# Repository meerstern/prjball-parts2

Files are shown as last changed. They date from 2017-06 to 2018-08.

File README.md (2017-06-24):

# prjball-parts2
Component Parts for ProjectionBall v5.X &amp; ProjectionBall  IoT

## 特徴 Feature
  * スマートフォンやPCからWifi経由で遠隔操作可能  You can control through phone or tablet.  
  * アナログ時計、デジタル時計を内蔵  The device has watch functions, digital and analog.  
  * 任意の文字列を表示可能(最大32文字、フォント内蔵)  The device has fonts. You can draw your favorite strings.  
  * 直径が10cm(旧モデル12cm)と一回り小さく  The diameter of this device is 10cm, it's smaller than previous one.   
  * Wifiはアクセスポイントモード、サーバモードの両対応  The wifi module has two modes, AP mode and server mode.  
  
## 関連リンク Related Links
  * ProjectionBall V5.X &amp; IoT [Firmware&Sourcecode][1]      
  * ProjectionBall V5.X &amp; IoT [STL Data&Gerber Data][2]  
  * ProjectionBall V5.X &amp; IoT [Wifi Module Sourcecode][3]  

  * Documents in English are in preperation.  
  * Please click Like button of [Projection Ball Page][4]. 
  
  License - MIT

  [1]: https://github.com/meerstern/prjball-firmware2 "*1"
  [2]: https://github.com/meerstern/prjball-parts2 "*2"
  [3]: https://github.com/meerstern/prjball-wifimodule2 "*3"
  [4]: https://www.facebook.com/projectionball "*4"

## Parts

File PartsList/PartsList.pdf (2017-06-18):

No. | Name | CNT | Memo | Link
1 | JST2PH10 Cables with PH Connector | 3 | Motor Cable& Laser | http://akizukidenshi.com/catalog/g/gC-05683/
2 | L-angle Pin header | 2 | | http://akizukidenshi.com/catalog/g/gC-01627/
2 | FA-130 Brushed Motor | 2 | Motor | https://www.sengoku.co.jp/mod/sgk_cart/detail.php?code=7BGF-TSM4
3 | Jumper | 2 | Wifi RX,TX
4 | CR2032 | 1 | RTCBattery
5 | Red Laser Module | 1 | | http://akizukidenshi.com/catalog/g/gM-00765/
6 | Mirror | 2 | Daiso Dental Mirror
7 | Cube Block　26xM6 | 2 | Mirror Anchorage | http://akizukidenshi.com/catalog/g/gP-07307/
8 | Brace | 2 | | https://www.sengoku.co.jp/mod/sgk_cart/detail.php?code=EEHD-0S35
9 | Bis M2.6x4 | 2
10 | Magnet　fai8x2 | 2 | Radial Magnet direction | https://www.26magnet.co.jp/webshop/cart.php?FORM_mode=view_goods_detail&FORM_goods_id=NE099
11 | Band | 5
12 | Sponge with Tape | 4 | D4mm x W15mm x L4M
13 | Acrylic Sphere 10cm | 1 | | http://amzn.asia/dPmUUdK
14 | Stand | 1 | | https://www.monotaro.com/p/0292/2376/?displayId=4
15 | USB Cable | 1 | | http://akizukidenshi.com/catalog/g/gC-09314/
17 | Capacitor 50V0.1uF | 2 | Noise protect for motor
*No.7,8,9 are not required when you use 3D ptinted mirror module, but two M3 Screw Nuts and two M2.6x6 bis.

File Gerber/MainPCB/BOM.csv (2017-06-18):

Elecrow PN | Parts | Value | Package | QTY | Digikey/Mouser/Manufacturer Part | Remark/ Link
 | JP6,JP11,JP12 | PH�@Male | THT | 3 | 455-1704-ND | Directions are written in silk pattern.
 | BT1 | BOX | CR2032V | 1 | 855-S8401-46
 | D1 | Diode | SMA | 1 | 863-MBR130T3G
C1644 | C1,C2 | 12p | 1608 | 2
C14663 | C7,C8,C9,C13,C14,C15,C16,C17,C18,C20,C5,C6,C3 | 0.1u | 1608 | 13
 | IC1 | 3.3VREG | v-reg-DPACK | 1 | 511-LF33CDT-TR
4040806A | LED1 | BULE | 1608 | 1
4041105A | LED2 | ORANGE | 1608 | 1
 | R5,R6 | VR | SMD | 2 | 81-PVZ3A472C01R00
C25804 | R7,R8,R9,R10,R14,R19,R20,R22,R4 | 10k | 1608 | 9
C21190 | R11,R12,R13,R21,R23,R24,R25,R26 | 1k | 1608 | 8
 | S1 | switch-TL3XYO | 1 | 612-EG1218
6030916A | JP5,JP13,JP15,JP16 | pinhead-1X02 | 4
 | U1 | STM32F373CB | LQFP-48 | 1 | 511-STM32F373CBT6
 | U2 | WIFI | ESP-13-WROOM-02 | 1 |  | Reauire a certification mark of conformance to technical standards in Japan.
 | Y1 | FC-135/32.K | ECS-31B_xtal | 1 | 732-FC135-32.76KAA3
 | C12 | 1000u | 810 | 1 | 647-UUD0J102MNL
 | C19 | 680u | 1010 | 1 | 647-UWT1A681MNL1GS
 | IC2 | DRIVER | SSOP24 | 1 | 757-TB6612FNGC8EL
 | S2,S3 | sw | THT | 2 | 688-SKHHBV
 | Q1 | NFET | SOT23 | 1 | 942-IRFML8244TRPBF
 | M2 | mSD | SMD | 1 | 798-DM3ATSFPEJM511
C15850 | C10,C11,C23 | 10u | 2012 | 3
 | F1 | PTC | 1812 | 1 | 507-1770-1-ND
 | M1 | uUSB CON | SMD | 1 | 649-10118194-0001LF

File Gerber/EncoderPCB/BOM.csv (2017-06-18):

Elecrow PN | Parts | Value | Package | QTY | Digikey/Mouser/Manufacturer Part | Remark/ Link
 | C2 | 0.1uF | 1608 | 1 | Free Components | 15331 | C14663
 | R1,R2,R3,R4,R5,R6 | 0 | 1608 | 6 | Free Components | 21903 | C21189
 | IC1 | AS5048A | TSSOP14 | 1 | AS5048A-HTSP-500CT-ND | http://www.digikey.jp/product-detail/ja/ams/AS5048A-HTSP-500/AS5048A-HTSP-500CT-ND/3188617

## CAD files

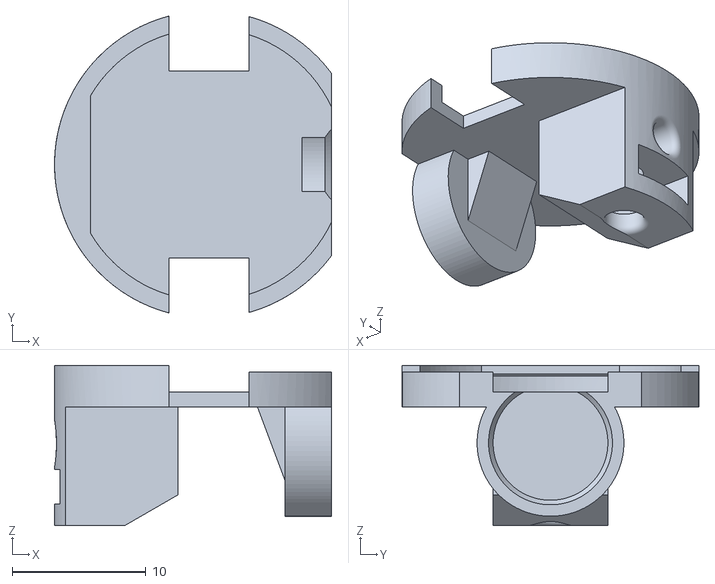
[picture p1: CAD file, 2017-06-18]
3DParts/mirror-module.stl
20.8 x 22.2 x 12.0

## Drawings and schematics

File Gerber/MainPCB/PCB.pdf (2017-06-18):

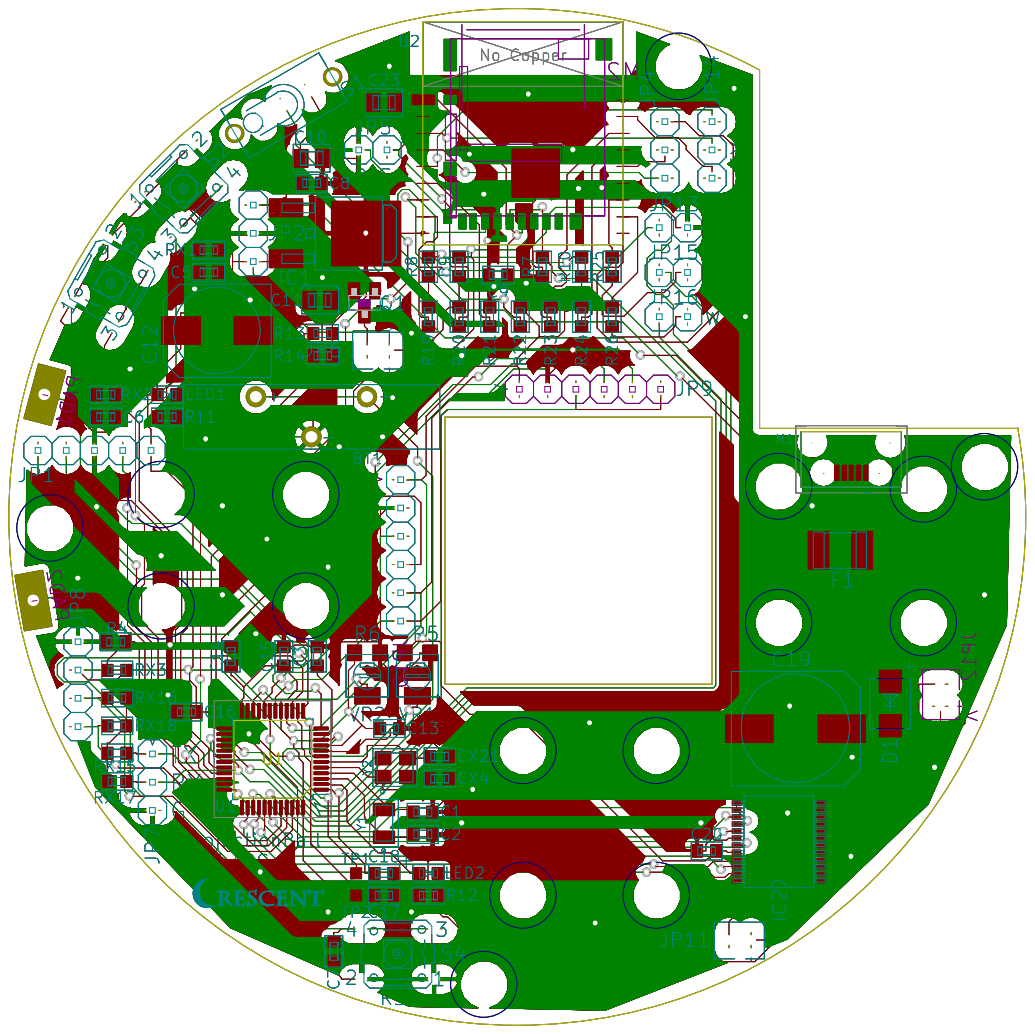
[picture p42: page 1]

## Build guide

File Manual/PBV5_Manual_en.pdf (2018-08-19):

# Projection Ball IoT

v5.4S

# User’s Manual

Revision
st 1 | 2017/04/19 | First release
nd 2 | 2017/6/10 | Add the way of adjustments

ProjectionBall Manual | 2

## Contents

1. Overview

Thank you for purchasing ProjectionBall this time. Please read this instruction manual carefully

and use it correctly.

It is a compact laser projector that anyone can use a laser projector which has been used only in

limited fields such as outdoor events by applying robot engineering technology at low cost.

ProjectionBall is a vector type simple laser projector. Drawing information is recorded at the time of

shipment, so you can draw immediately, such as stars and arrows.

By connecting the SD card slot, inserting the SD card with the data written in it, you can draw data

of your desired drawing shape from the SD card.
With the Wifi module (ESP - WROOM - 02), you can switch drawing from switching from smartphone

or PC to ProjectionBall, perform arbitrary character display, time adjustment, Wifi access point

setting etc is.

There is a Uart port shared with the Wifi module on the main body of ProjectionBall. You can also

operate ProjectionBall by connecting to Arduino, RaspberryPI etc via Uart port.

2. Safety Precautions

2-1. Prohibited items
◆ Prohibition of direct lighting of laser light

Although we are using a relatively safe laser module with class 2 output less than 1 mW, there is a

risk of loss of vision or loss of vision in direct viewing.

◆ Prohibition of projection to animals, people, especially head

We use a relatively safe laser module with class 2 output less than 1 mW, but if laser light enters the

eye directly, there is a danger of loss of vision or blindness.

◆ Supplied from PC USB power supply

Although USB connector is used as power supply, please never connect to PC. There is a possibility

that noise such as a motor etc. will enter the personal computer side and cause personal computer

malfunction.

2-2. Precautions

Do not use the USB power supply of output 1A or less

Operating power becomes insufficient, operation becomes unstable, it may cause breakdown at the worst. Please connect to USB charging adapter etc. (voltage 5 V, current 1.2 A or more).

◆ Please disconnect USB power after use

To prevent malfunction, please be sure to unplug the USB power supply or USB connector part after

use.

◆Please pay attention to strong magnets

A powerful neodymium magnet is used for the position detection in the mirror module part. There is

a possibility that it may cause trouble if it is brought close to a magnetic card or other equipment, so

please be careful about handling it.

◆ Place only drawing data on the SD card

When using the SD card please put only the drawing data in the card. In some cases, data in the card

may be damaged. Please do not use SD card with important data. Also, please use SD card with no

problem even if it is damaged.

3. Features

It is a compact laser projector that anyone can use a laser projector which has been used only in

limited fields such as outdoor events by applying robot engineering technology at low cost.

ProjectionBall is a vector type simple laser projector that can draw simple geometric figures and

alphanumeric characters. Because it uses a relatively safe laser light source, it is possible to project a

projection distance of about 1 m ahead in a bright place and about 5 m in a dark place.

◆ Excellent visibility

Because you are using a laser, you do not need to darken the room like a liquid crystal projector.

It is possible to draw clearly even in bright places.

◆ Design and functionality

Depending on the shape of the ball, it is possible to draw it anywhere you want, such as floor, wall, or

ceiling, in any orientation you like.

It operates with USB power supply and it is possible to draw for several hours with a mobile battery

for smartphone.

◆ Extensibility

By drawing any shape from the SD card and connecting it with a device such as RaspberryPI, it

becomes possible to draw your favorite figure at any time.

◆ Versatility

Not limited to the interior of the room, the application is infinite, such as digital signage such as

show window and reception, utilization as IoT display by other equipment cooperation, information

display by incorporating in the robot.

4. Specification
※ It may be changed
- Power supply 5 V, maximum 1.2 A microUSB terminal (Please supply from general purpose USB

power supply)

- Frame rate 5 to 15 fps (Depending on the number of coordinates, repeat number setting)
- Resolution mirror angle 9 degrees / 400 bit
- 10 types of built-in drawing data
- Alphanumeric display function (Scroll up to 30 characters maximum)
- Analog / digital clock, date display function
- SD card memory drawing (Maximum number of coordinates 200 points, up to 10 data can be

supported by switch switching)

- Micro SD card slot
- 3.3 V red 1 mW or less Class 2 laser module
- Blue power LED
- With Uart debug port (9600 bps, 3.3 V)
- Setting, time keeping function (backup battery CR 2032)
- Wifi module installed
- Capacitive touch sensor mounted

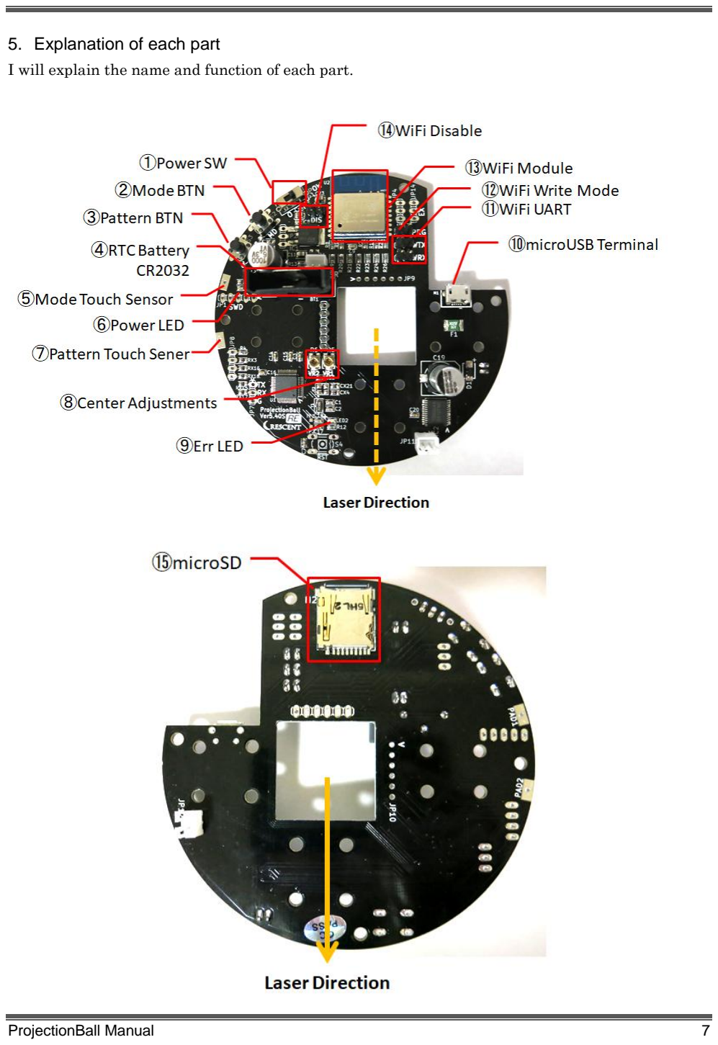
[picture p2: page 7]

5. Explanation of each part

I will explain the name and function of each part.

①Power switch

[0] turns OFF, [I] turns ON.

② Mode button

Switch on the mode such as constantly lighting,

strokes writing, clock etc.
③ Pattern button

Switch drawing patterns such as stars and

arrows.
④ Backup battery

Backup battery to store mode, pattern, character

string, time information.
⑤ Mode touch sensor

You can switch modes by touching a sphere. ⑥ Power LED

Blue lights up when the power is on.
⑦ Pattern touch sensor

Pattern can be switched by touching a sphere. ⑧ center adjustment trimmer

It is for adjusting the center axis of the mirror.

Please do not touch except when trouble such as

chipping occurs.
⑨ Error LED

It lights up when it stops automatic when there

is a problem with the mirror module or motor

part.

⑩ microUSB terminal

It is microUSB terminal for power supply. Please

use a power supply capable of supplying voltage

5V and current 1.2A.
⑪ WiFi UART pin

It is a jumper pin connecting the control

microcomputer and ESP - WROOM - 02.
⑫ WiFi write mode pin

When shorting the jumper and turning on the

power, ESP - WROOM - 02 goes into write mode. ⑬ WiFi module

It is ESP - WROOM - 02 which provides WiFi

function.
⑭ WiFi invalidation pin

Shorting off WiFi radio waves. It is used when

you want to invalidate WiFi communication in

environments where radio wave communication

is not permitted.
⑮ micro SD slot

Insert microSD containing data when drawing

from data created with drawing software.

6. How to use

This section explains how to prepare for using ProjectionBall.
① Assemble the stand. The side with the sponge will be on the upper side.

② Install the ProjectionBall main unit on the stand.

Check the laser irradiation destination. It is irradiated from the opposite part to the Wifi module.

If the ProjectionBall board is not set in the sphere, please set through the spherical cable hole with

the USB cable connected as shown below.

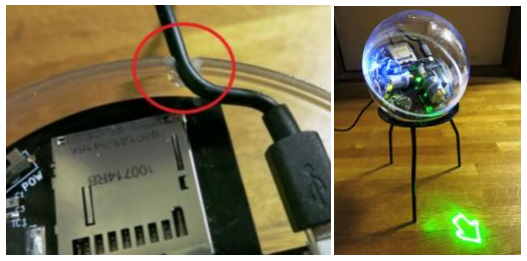
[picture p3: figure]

③Connect the USB power supply. Please use a USB power supply that can output a current of at

least 1.2 A with a voltage of 5 V.
④ The blue LED indicating power ON lights up, and drawing starts. If the blue LED does not light

up, check that the power switch on the Projection Ball main unit is ON.
⑤ To switch the drawing mode, touch the ProjectionBall main unit, the upper left, the mode touch

sensor near the palm. You can also press the mode button.

Lissajous mode → rotation mode → single stroke writing mode → continuous drawing mode →

analog watch mode→ digital watch mode → date display mode → character string display mode

Touch in this order to toggle.
⑥ To switch the drawing pattern, touch the ProjectionBall body, bottom left, touch the pattern touch

sensor with your palm. It is the same even if you press pattern button.

Star → arrow → e-mail → smile → sun → cloud → umbrella → snow → thunder

Touch in this order to toggle.

* When the microSD card containing the drawing data is inserted, the drawing data changes.
⑦ To temporarily stop drawing, touch the ProjectionBall body, upper left and lower left with the

palm at the same time. Touch the upper left and lower left with the palm again at the same time to

resume drawing. It is the same also with simultaneous pressing of pattern button and mode button. ⑧Turning the power ON while simultaneously holding the pattern button and pattern button

disables the touch function. If you turn on the power again while simultaneously pressing it, the

touch function will be activated.

7. Wifi connection method

ESP - WROOM - 02 for WiFi communication to the ProjectionBall main body is carried. It supports

two modes, server mode not via access point and client mode connecting via access point.

When it is used for the first time or when the configured access point can not be found, it is automatically connected directly (server mode). If a configured access point is found, it will

automatically go through the access point (client mode).

7-1. Server mode connection method
①Turn on the power of the Projection Ball.

When it is used for the first time or when the configured access point can not be found, it will

automatically enter the server mode in tens of seconds.
② Connect from the smartphone, PC, etc. to the access point name "prjballXX".

* The XX part is a unique alphanumeric character of a part of the MAC address of ESP - WROOM -

02.
③ Enter "192.168.4.1" to the address screen of the browser etc and press "Enter" key.

④ Connection is completed when "ProjectionBall Remote" screen is displayed.

※ Since the access point "prjballXX" is not connected to the Internet, the first connection on the

iPhone or Android smartphone may be disconnected immediately. Please repeat the connection

several times.

7-2. Client mode connection method
① Connect in advance in the above server mode and display "ProjectionBall Remote" screen.

② To connect via the access point, set "SSID" and "PASS" on the "Wifi" tab.

③ After completing the access point setting, it will be connected via the access point when the power

is turned on again.

* To connect via the access point, turn off the power of the Projection Ball once, then turn it on

again.

After several tens of seconds, we will automatically try to connect to the access point we set earlier.

If the connection is successful, you can operate from a browser such as a smartphone or PC

connected to the same access point.
④ On the address screen of the browser such as smartphone or PC

Type "prjballxx.local" and press "Enter" key. The XX part of prjballXX is the same as the XX part of

prjballXX of the access point name. The XX part is a unique alphanumeric character of a part of the

MAC address of ESP - WROOM - 02.
⑤ When "ProjectionBall Remote" screen is displayed, connection is completed.

If you want to connect again in the server mode, set appropriate characters with "SSID" and

"PASS" on the "Wifi" tab. .
※ Since you can not find an access point by entering appropriate characters, it will be in server

mode

7-3. ProjectionBall Remote How to use

I will explain how to use "ProjectionBall Remote" screen.

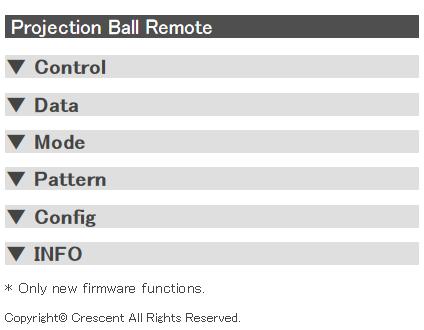
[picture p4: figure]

Immediately after displaying the "ProjectionBall Remote" screen, it is displayed in six categories:

"Control" "Data" "Mode" "Pattern" "Config" "Info".

◆ "Control" category

- "Start / Stop"

Please press "Stop" to pause drawing and "Start" to resume.

- "Angle"

It is used to change the drawing angle.

Enter the angle in the range of 0 to 359 °.

The angular resolution is 3 °.

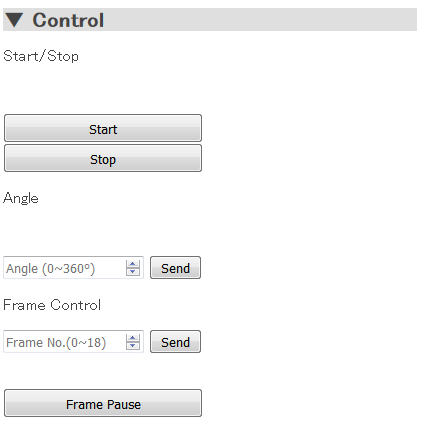
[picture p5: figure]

◆"Data" category

- "Internal / Memory Data"

To draw from the built-in drawing pattern, press "Internal Data".

To draw from the microSD containing the drawing data, press "Memory Data".

* If microSD is not inserted or drawing data is not inserted, drawing will stop when "Memory Data"

is pressed.

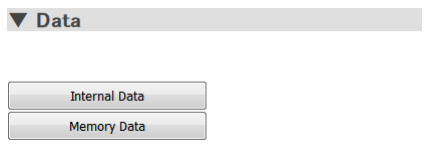
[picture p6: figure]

◆"Mode" category

- "Animation"

-MicroSD No card: Lissajous curve drawing
- With microSD card: animation drawing (frames **. Csv files are read in order)
- "Rotation"

It is a mode to draw while rotating.

- "One-stroke"

It is a mode to draw with a single stroke.

- "Always-on"

It is a mode to draw data all the time.

- "Analog Watch"

This mode displays the analog clock.

- "Digital Watch"

This mode displays the digital clock.

- "Date"

It is a mode to display the date.

- "String"

This mode displays alphanumeric character strings. The initial value is "Hello".

You can draw an arbitrary character string by filling in "String" field and pressing "Send" button.

* If it is more than 6 characters it will be automatically scrolled and rendered.

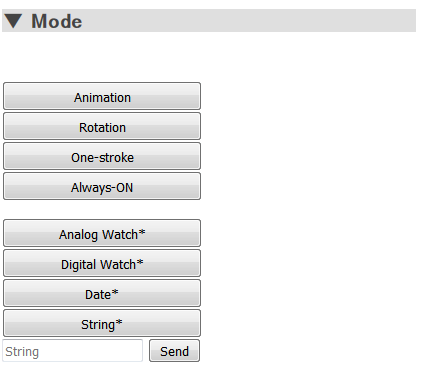
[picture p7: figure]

◆"Pattern" category

Drawing stops if there is no corresponding drawing data even with microSD card.

- "Star / Data 0"

-MicroSD card absent: The star of the built-in data is drawn.

-Micro SD card present: data0.csv file will be drawn.

- "Star / Data 0"

-MicroSD card absent: The star of the built-in data is drawn.

-Micro SD card present: data0.csv file will be drawn.

- "Arrow / Data 1"

-MicroSD card absent: Arrow of internal data will be drawn.

-Micro SD card present: data1.csv file will be drawn.

- "Mail / Data 2"

-MicroSD card absent: Mail of internal data will be drawn.

- With microSD card: data2.csv file will be drawn.
- "Smile / Data 3"

-MicroSD No card: Smile of internal data will be drawn.

-Micro SD card present: data3.csv file will be drawn.

- "Sun / Data 4"

-MicroSD card absent: The sun of the built-in data is drawn.

-Micro SD card present: data4.csv file will be drawn.

- "Cloud / Data 5"

-MicroSD card absent: Cloud of built-in data will be drawn.

-Micro SD card present: data5.csv file will be drawn.

- "Rain / Data 6"

-MicroSD card absent: umbrella of internal data will be drawn.

-Micro SD card present: data6.csv file will be drawn.

- "Snow / Data 7"

-MicroSD card absence: snow of built-in data is drawn.

-Micro SD card present: data7.csv file will be drawn.

- "Thunder / Data 8"

-MicroSD card absence: Lightning of built-in data will be drawn.

-Micro SD card present: data8.csv file will be drawn.

- "Heart / Data 9"

-MicroSD card absent: Heart of built-in data will be drawn.

- With microSD card: data9.csv file will be drawn.

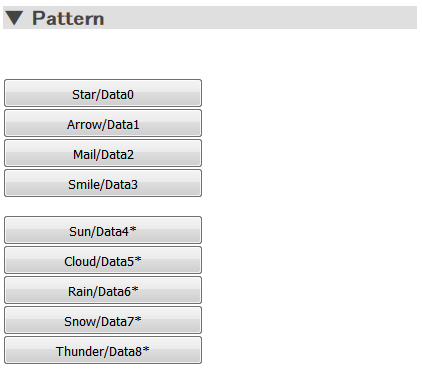
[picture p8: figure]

◆"Config" category

Set WiFi module access point settings, date and time.

- "WiFi AP Mode Setting"
Connect using the access point Set the access point name (SSID) and password (PASS) when using

client mode. After inputting and pressing "SAVE", the setting is saved.

- "Set Date"

To set the date, press "Send". The dates acquired from browsers such as smartphones and PCs are

automatically entered.

* If the date is not displayed properly, check the date of the smartphone or PC you are operating.

- "Set Time"

To set the time, press "Send". Time is automatically entered from the browser such as smartphone or

PC.

* If the time is not displayed correctly, check the time of the smartphone or PC you are operating.

◆"Info" category

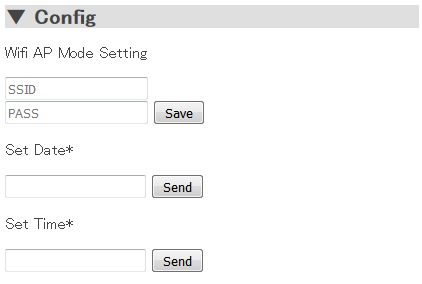
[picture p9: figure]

The Wifi module version and Web site link are displayed.

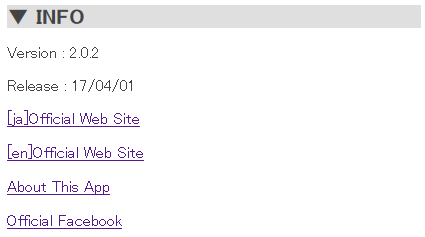
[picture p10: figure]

8. Optional data drawing method

You can draw drawing data on the SD card, slot it on the board, and draw arbitrary shapes.

8-1. SD card drawing specification

- When the SD card is not inserted, it will automatically draw from the internal memory data of the

main unit.

- If an SD card is inserted and drawing data is not inserted or if the file is corrupted, an error occurs

and nothing is drawn.

- Pattern drawing specification
- Up to 10 types of drawing can be made by switching pattern switches.
- It is possible to select from 3 types of constantly lit, rotated, and stroked by mode switch switching.
- The maximum number of coordinates per file is 200.
- File name is half-width alphanumeric data0.csv data1.csv data2.csv data3.csv ... data9.csv.
- Animation drawing specification
- By inserting drawing data slightly different from frame 0 to frame ** (maximum ** up to 17)

animation drawing like a flip cartoon becomes possible.

- Insert the file corresponding to the SD card, and place it under the mode switch SW4 or SW5, the

animation drawing will start.

- The maximum number of coordinates per file is 200.
- File name must be half-width alphanumeric, frame0.csv frame1.csv · · · frame 18. csv.
- Approximately every 300 msec, the drawing data will be switched automatically from frame 0 to

frame 1, frame 2 and according to the number of files in the SD card.

- It returns to frame 0 in the last file and it operates iteratively.

8-2. Drawing data creation method

In this section, we will explain the drawing data creation method using dedicated drawing data

creation software.

Please download the drawing software from the following URL.

http://projectionball.jp/share/PBS.zip pass: crescent

- The operating environment is Windows .Net Framework 4.5 or later installed PC
- Launch PBS 2.exe by double-click with no installer required.
- Drawing data creation method using dedicated drawing software
1) Activate the software.
2) Place new coordinates by left clicking and create your favorite shape. Conversely, when deleting,

you can delete the coordinates by right clicking.
3) Please arrange the coordinates finely for curves and complicated figures. Also, please set so that

the starting point and the ending point are close.
4) When finished, save as "File" → "Save As" → "pbs file".

5) Select "File" -> "export csv" -> "data0.csv" and export.
6) Save the "data0.csv" file on the SD card, set it under SW2, SW3 down, SW4 up and SW5, and

when you turn on the power, the figure will be drawn.
※ Note Even if pbs file is saved on SD card, it can not be drawn. Please export the csv file and save it

on the SD card.

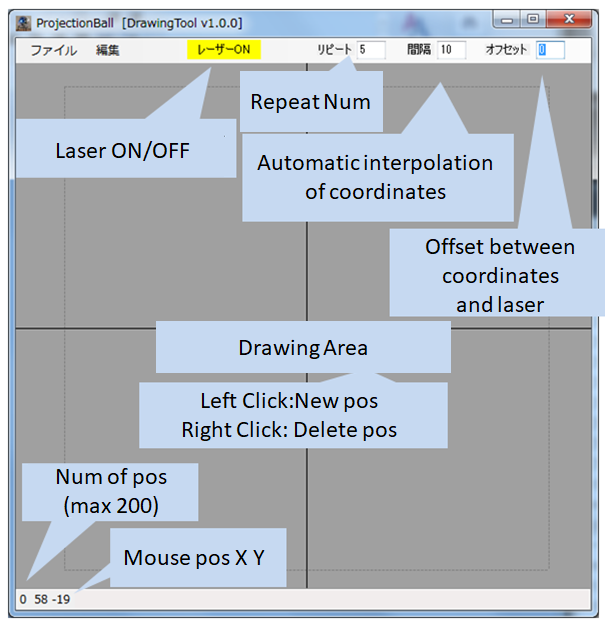
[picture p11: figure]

- As the repeat number increases, the accuracy increases but the frame rate becomes rough.

Conversely, if the repeat number is small, the accuracy will be worse, but the frame rate will rise. If

the repeat number 5 is a standard and complicated figure, set it to 8 to 12. Conversely, in case of

simple figure, set repeat number to 3 ~ 5.

- To move the middle coordinates, hold down the "Ctrl" key and drag the coordinates you want to

move to move the middle coordinates.

- To place new coordinates, hold down the "Shift" key and left click to place the coordinates in laser

OFF mode.

- If the starting point and the ending point can not be located close to each other, click "Laser ON /

OFF", turn OFF the laser lighting, and put the extinct coordinates so that the end point is near the

starting point.

- If there is an image file of the figure you want to draw, place the background with "Edit" →

"Background reading".

* If the size does not match please edit the image file with "paint" etc and resize it.

- If a message with more than 200 drawing coordinates appears at the time of export, reduce the

number of coordinates or set the interval to a larger value such as 10 to 20 of the initial value.

- On the improvement of accuracy of drawing data
- If you want to draw at sharp corners, arrange the corner part coordinates a few times consecutively

and place them at the same place and the corners will be drawn cleanly.

- It is also possible to draw beautifully by making the acute angle part circle around and letting the

detour part "laser off".

8-3. Drawing data specification

Describe the specification of drawing data. The csv file created with dedicated drawing software

meets the following specifications. Please refer if you do not use special drawing software.

- In the first line, enter the numerical value for drawing definition. In the first row and the first

column, enter the repeat number.

Please enter 0 for 1st row 2nd row, 3rd row. If 5 is standard and complicated figure, set it to 8 ~ 12.

For simple figures, set the repeat number to 3 ~ 5.

- As the repeat number increases, the accuracy increases but the frame rate becomes rough.

Conversely, if the repeat number is small, the accuracy will be worse, but the frame rate will rise.

- From the 2nd line, enter coordinate data with half-width numerals.
- The first row indicates whether or not the laser is lit, 0 is off, and 1 is lit.
- The second row is the X coordinate and the third row is the Y coordinate.
- Create coordinates with a maximum (± 150, ± 150) around (0,0) as a guide.
- When the drawing starts, the laser light moves from the 2nd line to the 3rd line and the 4th line

sequentially.

- If you find a blank space, judge it as the last data, go back to the second line and start drawing

again.

* In the case of dedicated drawing software, it automatically becomes data according to the following

rule

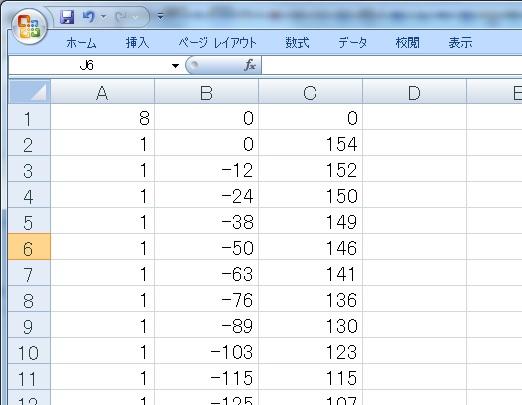
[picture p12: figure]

9. How to rewrite WiFi module

ESP - WROOM - 02 for WiFi communication to the ProjectionBall main body is carried. The factory

shipped ESP - WROOM - 02 code is published on the following site. If necessary, you can also update

your ESP - WROOM - 02 or add your own code by adding it.

https://github.com/meerstern/prjball-wifimodule 2

Also, IO pins other than the RX and TX ports used in ProjectionBall can be accessed from the

external EX port. It is possible to connect LED and serial communication equipment separately as

necessary.

9-1. Arduino development environment preparation

We use the Arduino development environment when updating the firmware of ESP - WROOM - 02 or

incorporating your own code.
① Install the Arduino development environment on the PC.

② Activate the Arduino development environment and click "File" → "Development environment".

③ Add the following URL to "Additional Board Manager URL" on the "Settings" tab.

http://arduino.esp8266.com/stable/package_esp8266com_index.json

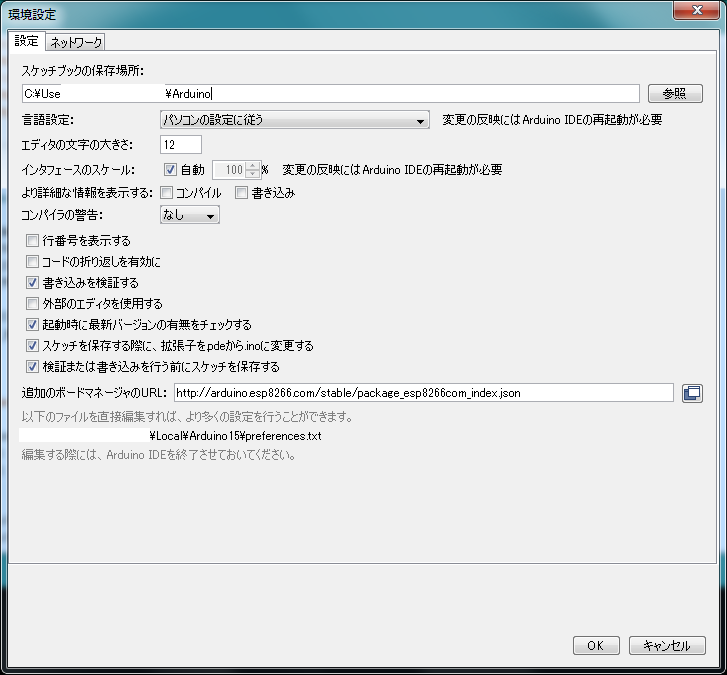
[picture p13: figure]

④Scroll from Tools -> Microcomputer Board -> Board Manager to the bottom, select 'esp 8266 by

ESP 8266 Community' and click Install.

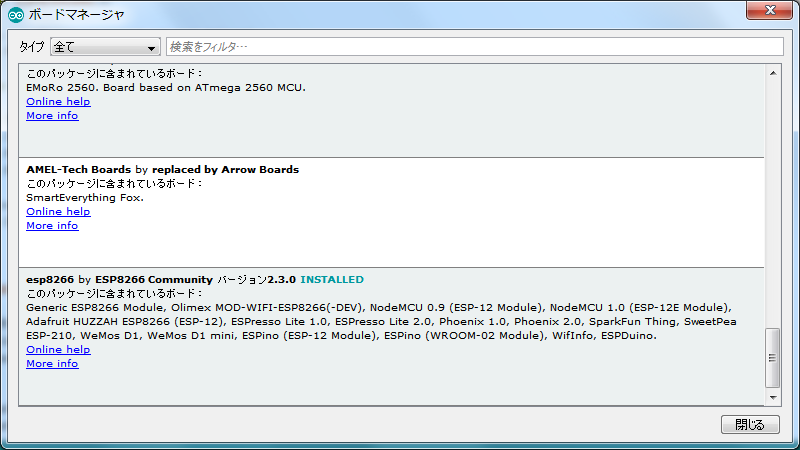
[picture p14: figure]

⑤Click "Tools" → "Microcomputer board" → "Generic ESP 8266 Module".

⑥ Perform the setting as described below in "Tool" → "Microcomputer board".

The serial port selects the serial port connected to ESP - WROOM - 02 at the time of writing.

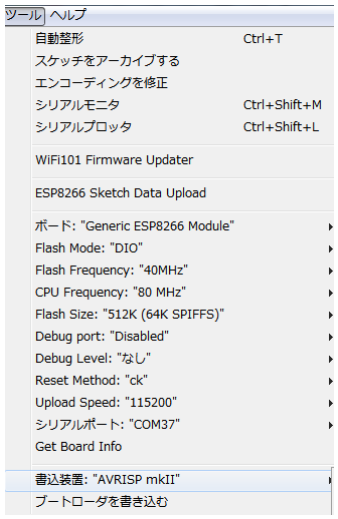
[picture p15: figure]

9-2. Writing from the Arduino development environment

When writing the firmware from Arduino development environment to ESP - WROOM - 02, a USB

serial conversion module etc is required. Please prepare separately.
USB serial conversion module (AE-FT 234 X) http://akizukidenshi.com/catalog/g/gM-08461/

① Remove the jumper pin to WiFi UART TX pin and WiFi UART RX pin,

Connect the USB serial conversion module to the ESP - WROOM - 02 of the Projection Ball main

unit. In case

Connect the GND of the USB serial conversion module to the WiFi UART GND pin.

Connect the USB serial conversion module TX to the WiFi UART RX pin.

Connect the USB serial conversion module RX to the WiFi UART TX pin.

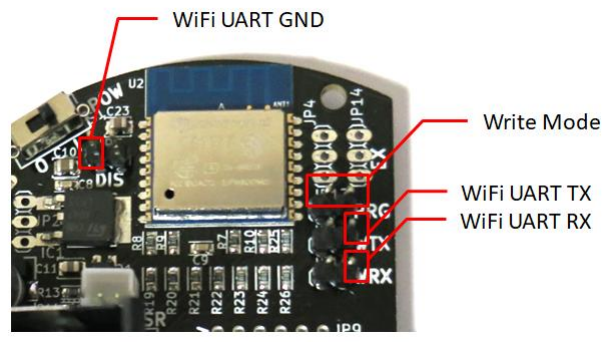
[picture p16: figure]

②Confirm the port number of the USB serial conversion module from the device manager etc.

③ Download the latest WiFi module firmware code from the site below and open the "ESP8266.ino"

file.

https://github.com/meerstern/prjball-wifimodule 2
④ Set the port number of the USB serial conversion module.

Select the connection destination port from "Tools" → "Serial port".
⑤ Connect the jumper to the write mode pin and short the write mode pin.

⑥ Power on the Projection Ball body.

⑦ Press the write button to write the farm.

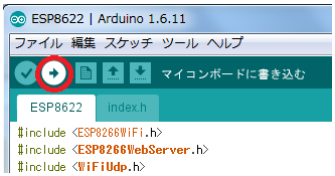
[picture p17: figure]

⑧It is update when writing is completed.

In case of first time writing, an error may appear.
If you get an error please try again while confirming the work from ①.

⑨ Set the jumper pin to WiFi UART TX pin (WiFi UART RX pin if necessary).

10. External device linkage method

By sending commands from the UART port of ProjectionBall to the UART port of another device, it is

possible to switch the drawing pattern and drawing mode, pause the drawing, and reread the

drawing data.

If necessary, connect pinhaders and wiring and connect to other equipment. Connect the TX on the

board to the RX terminal of another device, the RX on the board to the TX terminal of another device,

and also connect the GND.
When sending a command from a PC etc., use a USB serial conversion module (AE - FT 234 X

http://akizukidenshi.com/catalog/g/gM-08461/ ) etc and send a command using COM software such as

Teraterm please.
After sending the command, the command is executed by sending the return key (line feed). The

voltage of UART is 3.3V. It is different from RS232C. Also, please set the baud rate to 9600 bps.

* In the case of external device linkage, since the UART ports conflict, the command command from

the WiFi module can not be used.

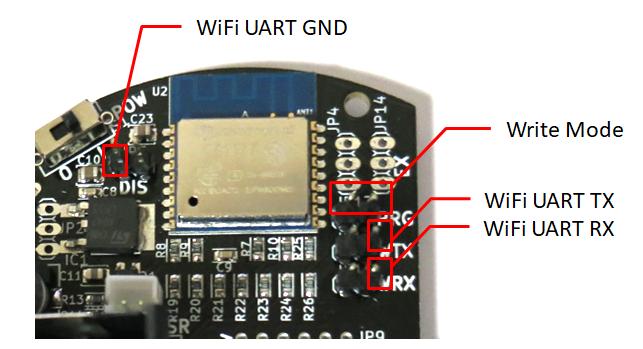
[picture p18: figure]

Table 1 UART Command lists

Command Name | Uart command | Description
Start | srt | When drawing is stopped by a command, it is used again when restarting.
Stop | stp | It is used to stop drawing.

Pattern0 | sw0 | No SD card star pattern, with SD card data0.csv drawing
Pattern1 | sw1 | No SD card arrow pattern, with SD card data1.csv drawing
Pattern2 | sw2 | No SD card mail pattern, with SD card data2.csv drawing
Pattern3 | sw3 | No SD card smile pattern, with SD card data3.csv drawing
Pattern4 | sw4 | No SD card sun pattern, with SD card data4.csv drawing
Pattern5 | sw5 | No SD card cloud pattern, with SD card data5.csv drawing
Pattern6 | sw6 | No SD card rain pattern, with SD card data6.csv drawing
Pattern7 | sw7 | No SD card snow pattern, with SD card data7.csv drawing
Pattern8 | sw8 | No SD card thunder pattern, with SD card data8.csv drawing
Pattern9 | sw9 | No SD card heart pattern, with SD card data9.csv drawing
Analog Clock | awt | Switch to analog clock display mode.
Digital Clock | dwt | Switch to digital clock display mode.
Date Mode | dym | The date display mode is switched.
String Mode | stm | Switch to arbitrary character string display mode.
String Set | stg=X | Arbitrary alphanumeric characters are displayed by placing an alphanumeric character string in X. X can be up to 30 characters.
Time Set | tim=XXYYZZ | Set the time via the UART. Example tim = 213000 21h:30m:00s
Time Get | tim? | Currently, the time held inside ProjectionBall is returned in UART.
Date Set | day=XXYYZZ | Set the date via UART. Example day = 170401 17’April, 1st
Date Get 令 | day? | The date currently held in ProjectionBall is returned in UART.
Animation Mode | frm | No SD card :Lissajous curve With SD card : animation (frame **. Csv) will be.loaded.
Rotate Mode | rot | Switch to the rotating animation drawing mode.
Stroke Line Write Mode | str | Switch to the stroke writing animation drawing mode.
Always Lighting Mode | alw | It switches to the drawing mode that always lights up.
Center Position Setting | cen=X,Y | By inserting numbers into X and Y, it is a command to move relative to the current drawing coordinate center. If you set a large value, drawing may not be done correctly. Examples cen = 20, -30
Angle Setting | deg=X | By inserting a value from 0 ° to 360 ° in X, this command rotates the drawing figure at 3 ° intervals. Example deg = 135
Reload | rst | This command executes reading again when the SD card is replaced.
Frame Specification | fno=X | By placing a value between 0 and 18 in X, we draw the frame of the specified animation.
Animation Drawing Frame Pause | fpa | Stops automatic feeding of drawing data when animation is drawn. By running the same command again, automatic feed is restarted.

11. Laser module specification

In terms of safety, we are using a red laser module with 3.3 V drive that is less than 1 mW. When

replacing with another laser module, the same 3.3 V laser module can be used. The maximum

current that can be supplied is 250 mA as designed. We can not support problems and failures due to

the use of laser modules other than standard products.

12. Adjust / Troubleshoot

When trouble etc. occurred, please refer to the following. ◆ The power LED lights, but drawing does not start

- In case of pause mode, release it

Touch the ProjectionBall body, upper left and lower left with the palm at the same time. Touch the

upper left and lower left with the palm again at the same time to resume drawing. It is the same also

with simultaneous pressing of pattern button and mode button.

- Check that the current of the USB power supply is sufficient enough.
Please connect to USB charging adapter etc. (voltage 5 V, current 1.2 A or more).

◆ Mode, pattern, time etc. are reset

It is possible to hold for more than a few months without USB power supply.

If mode, time etc. are not maintained, please replace the battery.

Replacement battery CR 2032 x 1 * Please be sure to replace plus / minus polarity with care.

◆ WiFi access point is not displayed, can not connect

- Check that there is no jumper pin on the WiFi invalidation pin of the ProjectionBall main unit.

When a jumper pin is inserted in the WiFi invalidation pin, the radio wave stops and can not be

connected.

- If there are multiple other WiFi radio waves in the vicinity, it may not be possible to connect due to

interference or interference.

Please connect the PC or smartphone closer to the ProjectionBall main unit.

◆ Drawing is lacking

- Make sure that the laser beam strikes the stand, the sphere, etc., and is not blocked.
- The center position of the drawing may be misaligned.

When the drawing center position shifts, the optical axis of the laser interferes with the frame part,

and the drawing is lacking. First adjust the position of the motor and laser module so that the optical

axis of the laser reflects at the center of the mirror. If it still does not come to the center, adjust the

variable resistance.

Adjust the variable resistor VR 1, 2 for drawing center adjustment with the + driver. Adjust the angle, please turn. If the laser beam does not hit the center of the mirror (back side) of the motor 2, adjust the center of the motor 1 (X axis direction) by adjusting VR1. When the laser light emitted

from the motor 2 is caught on the board, adjust the center of the motor 2 (Y axis direction) by

adjusting VR2.

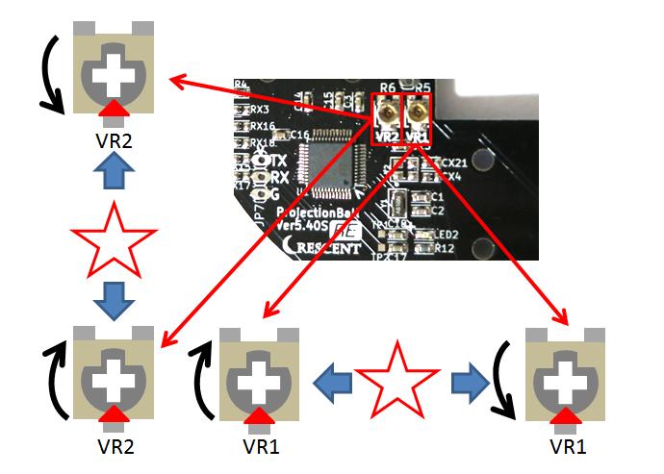
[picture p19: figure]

◆The shape is randomly drawn or the drawing is not clean

- When the current of the power supply is insufficient or the current is limited by the safety circuit of

the USB charging adapter, it may not operate properly. Please try another USB power supply.

- Mirror position Make sure that the center of the magnet matches the center of the encoder IC (black chip of the encoder board). Also check whether the distance between the magnet and the

encoder IC is about 5 mm. On the contrary, if it is too close, contact and magnetic force may be too

strong to draw beautifully.

◆ Error Yellow Lights up and stops

- Make sure that motor 1 and motor 2 are properly connected to the connector. Make sure that the

encoder board is correctly soldered. Also, make sure that the metal of the housing of the laser module

contacts the soldering part of the encoder board and is not short-circuited.

◆ Mirror module magnet position adjustment method

This adjustment has already been done at shipment. Do not remove the magnet from the mirror

module.

In the unlikely event that you remove the magnet from the mirror module, follow the procedure

below to adjust the magnet position.

A neodymium magnet for position detection is installed on the side opposite to the motor shaft mounting part of the mirror module (red frame in the figure below). Unlike ordinary magnets, this neodymium magnet has NS poles separated in the axial direction. The boundary between N pole and

S pole is detected with a sensor and the position is read. If the angle of this magnetic pole is deviated

from the reflection surface of the mirror, it will not be drawn at the intended location.

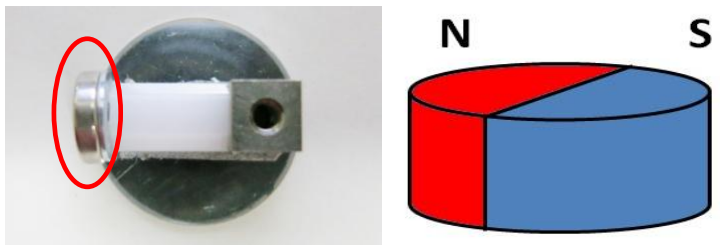
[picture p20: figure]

* If one side is mounted correctly, it is possible to fix the magnet so that the two sides of the

magnet face each other so that the magnets face each other.

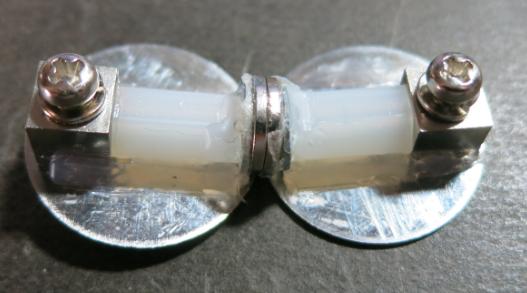
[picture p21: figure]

① Place the mirror module at the center of the azimuthal magnet with the magnet part of the

mirror module facing downward (be careful as the azimuthal magnet goes bad if placed for a

long time).

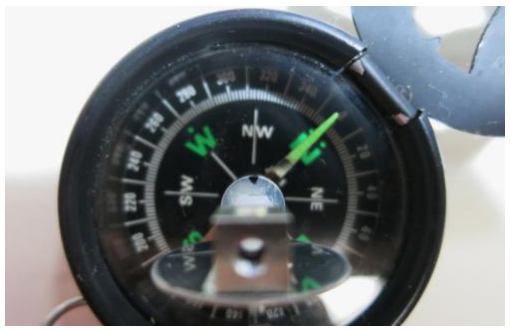
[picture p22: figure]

② As shown in the figure below, rotate the magnet adsorbed by the washer so that the N pole of

the azimuthal magnet faces to the left, and make the angle of the azimuthal magnet coincide with the mirror surface. When the adjustment is completed, fix it with tape).

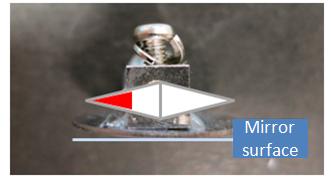
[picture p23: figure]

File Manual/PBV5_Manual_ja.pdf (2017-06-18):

# Projection Ball IoT

v5.4S

# 取扱説明書

改訂履歴

第 1 版 | 2017/04/19 | 新規作成
第 2 版 | 2017/6/10 | 調整方法及び誤字を修正

ProjectionBall 取扱説明書 | 2

目次

1. 概要

このたびは ProjectionBall をお求め頂き、ありがとうございます。本取扱説明書をよくお読みいただき、 正しくご使用ください。
今まで野外イベントなど限られた分野でしか使われていなかったレーザープロジェクタをロボット工 学の技術を応用し、低価格で誰でも使える小型レーザープロジェクタです。 ProjectionBall はベクター方式の簡易レーザープロジェクタです。出荷時に描画情報が記録されている ため、星や矢印などすぐに描画を行うことができます。
SD カードスロットを接続し、データを書き込んだ SD カードを挿入して起動することで、SD カードか ら好きな描画形状のデータを描画することもできます。

Wifi モジュール(ESP-WROOM-02)を搭載しているため、スマートフォンや PC から ProjectionBall へ接 続して、描画切替を行うことや任意の文字表示、時刻調整、Wifi アクセスポイント設定などを行うこと が可能です。

Wifi モジュールと兼用の Uart ポートが ProjectionBall 本体にあります。Uart ポートを介して Arduino や

RaspberryPI 等と接続して、ProjectionBall を操作することもできます。

2. 安全上のご注意

ご使用の前に本章をよくお読みの上、正しくお使いください。

2-1. 禁止事項
◆レーザー光の直視禁止
クラス 2 出力 1mW 以下の比較的安全なレーザーモジュールを使用していますが、直視は視力低下や 失明の危険性があります。

◆動物、人、特に頭部への投影禁止
クラス 2 出力 1mW 以下の比較的安全なレーザーモジュールを使用していますが、直接目にレーザー 光が入った場合、視力低下や失明の危険性があります。

◆パソコン USB 電源から供給禁止
電源として USB コネクタを使用していますが、絶対にパソコンには接続しないでください。パソコン 側にモータ等のノイズが入りパソコン故障の原因となる可能性があります。

2-2. 注意事項
◆出力 1A 以下の USB 電源使用しないこと
使用電力が足りず、動作が不安定になり、最悪、故障の原因となる場合があります。USB 充電用のア ダプタ等(電圧 5V、電流 1.2A 以上)に接続して使用してください。

◆使用後は USB 電源を外してください
誤動作防止のため、使用後は必ず USB 電源もしくは USB コネクタ部を抜いてください。

◆強力な磁石に注意してください
ミラーモジュール部には位置検出のために強力なﾈｵｼﾞﾑ磁石を使用しています。磁気カードや他の機器 に近づけると不具合を起こす可能性がありますので、取扱いに気をつけてください。

◆SD カードには描画データのみ入れること
SD カードを使用する際にはカード内には描画データのみを入れてください。場合によりカード内のデ ータが破損する可能性もあります。大切なデータの入った SD カードを使用しないでください。また、万 一、破損しても問題のない SD カードをご使用ください。

3. 特徴

今まで野外イベントなど限られた分野でしか使われていなかったレーザープロジェクタをロボット工 学の技術を応用し、低価格で誰でも使える小型レーザープロジェクタです。 ProjectionBall はベクター方式の簡易レーザープロジェクタで、簡単な幾何図形や英数字などを描画す ることが可能です。比較的安全なレーザー光源を使用しているため、明るい場所では投影距離は約 1m 先、 暗い場所では約 5m 程度先まで投影することが可能です。

◆優れた視認性
レーザーを使用しているため、液晶プロジェクタのように部屋を暗くする必要がありません。 明るい場所でもはっきりと描画することが可能です。

◆デザインと機能性
ボール形状により、床や壁、天井など好きな向きに好きな場所に描画することが可能です。 USB 電源で動作し、スマートフォン用モバイルバッテリで数時間以上描画することが可能です。

◆拡張性
SD カードから好きな図形を描画することや RaspberryPI などのデバイスとつなげることにより、好 きなタイミングで好きな図形を描画することが可能になります。

◆汎用性
部屋のインテリアに限らず、ショーウィンドウや受付などのデジタルサイネージ、他機器連携による IoT ディスプレイとしての活用、ロボットに組込んで情報表示など用途は無限です。

4. 仕様

※変更する場合があります
・電源 5V、最大 1.2A microUSB 端子(汎用 USB 電源から給電してください) ・フレームレート 5~15fps(座標数、リピート数設定に依る) ・分解能ミラー角 9 度/400bit
・内蔵描画データ 10 種類
・英数字表示機能(スクロールで最大 30 文字程度)
・アナログ/デジタル時計、日付表示機能
・SD カードメモリ描画(最大設定座標数 200 ポイント、スイッチ切り替えで最大 10 データまで対応) ・マイクロ SD カードスロット
・3.3V 赤色 1mW 以下 Class2 レーザーモジュール
・青色電源 LED

・Uart デバッグポート付(9600bps、3.3V) ・設定、時刻保持機能(バックアップ電池 CR2032) ・Wifi モジュール搭載
・静電容量タッチセンサ搭載

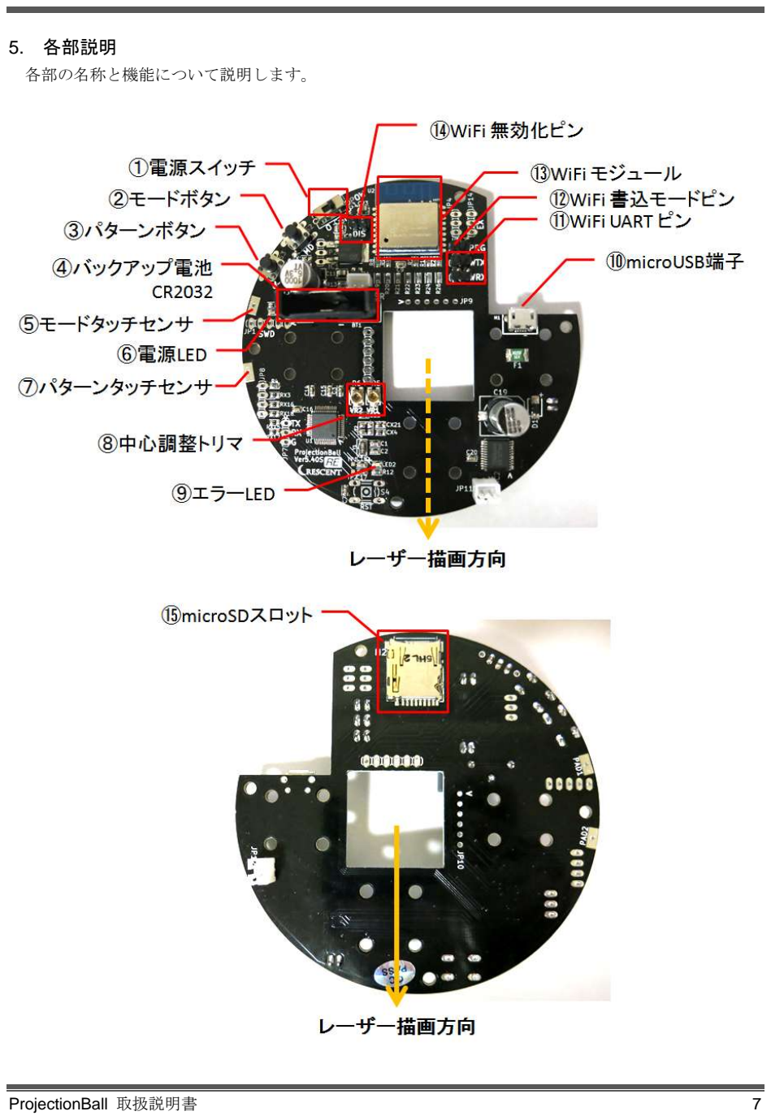
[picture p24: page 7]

5. 各部説明

各部の名称と機能について説明します。

①電源スイッチ
[0]で OFF、[Ⅰ]で ON になります。
②モードボタン
常時点灯や一筆書き、時計などのモードを切り替
えます。
③パターンボタン
星や矢印など描画パターンを切り替えます。
④バックアップ電池
モードやパターン、文字列、時刻情報を記憶する
ためのバックアップ電池です。
⑤モードタッチセンサ
球体をタッチすることでモード切替できます。
⑥電源 LED
電源 ON で青色が点灯します。
⑦パターンタッチセンサ
球体をタッチすることでパターン切替できます。
⑧中心調整トリマ
ミラーの中心軸の調整用です。描画が欠ける等の
不具合時以外は触れないでください。
⑨エラーLED
ミラーモジュールやモータ部分に不具合があっ
た場合に自動停止すると点灯します。

⑩microUSB 端子
電源供給用の microUSB 端子です。電圧 5V、電 流 1.2A 供給可能な電源を使用してください。

⑪WiFi UART ピン
制御用マイコンと ESP-WROOM-02 を接続する ジャンパピンです。
⑫WiFi 書込みモードピン
ジャンパをショートさせて電源を入れると
ESP-WROOM-02 が書込みモードになります。 ⑬WiFi モジュール

WiFi 機能を提供する ESP-WROOM-02 です。 ⑭WiFi 無効化ピン
ショートさせると WiFi 電波を停波します。無線
電波の通信が認められていない環境や WiFi 通信を 無効化したい場合に使用します。

⑮microSD スロット
描画ソフトウェアで作成したデータから描画す
る場合にデータの入った microSD を挿入します。

6. 使用方法

ProjectionBall の使用開始するための準備方法について説明します。
① スタンドを組み立てます。スポンジが付いている面が上側となります。

② ProjectionBall 本体をスタンドへ設置します。
レーザーの照射先を確認します。Wifi モジュールとは逆の部分から照射されます。
球体内に ProjectionBall 基板がセットされていない場合は USB ケーブルを接続した状態で下記のよ うに球体のケーブル穴を通してセットしてください。

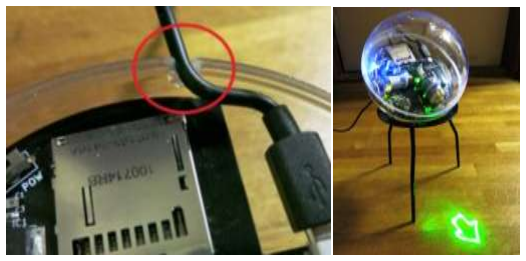
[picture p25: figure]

③ USB 電源を接続します。電圧 5V、出力 1.2A 以上の電流が出せる USB 電源を使用してください。 ④ 電源 ON を示す青色 LED が点灯し、描画が開始されます。青色 LED が点灯しない場合は ProjectionBall 本体の電源スイッチが ON であるか確認してください。
⑤ 描画モードを切り替える場合は ProjectionBall 本体、左上、モードタッチセンサ付近を手のひらで タッチしてください。モードボタンを押しても同じです。 リサージュモード→回転モード→一筆書きモード→常時描画モード→アナログ時計モード →デジタル時計モード→日付表示モード→文字列表示モード の順にタッチする毎に切り替わります。
⑥ 描画パターンを切り替える場合は ProjectionBall 本体、左下、パターンタッチセンサ付近を手のひ らでタッチしてください。パターンボタンを押しても同じです。 星→矢印→メール→スマイル→太陽→雲→傘→雪→雷
の順にタッチする毎に切り替わります。
※描画データの入った microSD カードが挿入されている場合は描画データが切り替わります。 ⑦ 描画を一時停止する場合は ProjectionBall 本体、左上と左下を同時に手のひらでタッチしてくださ い。再度、左上と左下を同時に手のひらでタッチすると描画を再開します。パターンボタンとモー ドボタンの同時押しでも同様です。

⑧ パターンボタンとパターンボタンを同時に押しながら電源 ON にするとタッチ機能が無効化します。 再度、同時に押しながら電源 ON にするとタッチ機能が有効化されます。

7. Wifi 接続方法

ProjectionBall 本体に WiFi 通信するための ESP-WROOM-02 を搭載しています。アクセスポイントを経 由しないサーバモードとアクセスポイントを経由して接続するクライアントモードの 2 つに対応してい ます。
初回使用時及び設定済みアクセスポイントが見つからない場合は自動的に直接接続(サーバモード)と なります。設定済みのアクセスポイントが見つかった場合は自動的にアクセスポイント経由(クライアン トモード)となります。

7-1. サーバモード接続方法

①ProjectionBall の電源を入れます。
初回使用時及び設定済みアクセスポイントが見つからない場合は数十秒後に自動的にサーバモー ドになります。
②スマートフォンや PC 等からアクセスポイント名「prjballXX」へ接続してください。
※XX 部分は ESP-WROOM-02 の MAC アドレスの一部分の固有な英数字です。 ③ブラウザ等のアドレス画面へ「192.168.4.1」を打ち込んで「Enter」キーを押してください。 ④「ProjectionBall Remote」画面が表示されたら、接続完了です。 ※アクセスポイント「prjballXX」はインターネットに接続されていないため、iPhone や Android 等のスマートフォンでは最初の接続はすぐに切断されてしまう場合があります。何度か接続を繰 り返してください。

7-2. クライアントモード接続方法
①予め上記のサーバモードで接続し、「ProjectionBall Remote」画面が表示させてください。 ②アクセスポイント経由で接続する場合は「Wifi」タブの「SSID」「PASS」を設定してください。 ③アクセスポイント設定完了後、電源再投入でアクセスポイント経由で接続されます。 ※アクセスポイント経由で接続するため、ProjectionBall の電源を一度切ってから再度入れます。 数十秒後に自動的に先ほど設定したアクセスポイントへ接続を試行します。 接続が成功した場合すると同一のアクセスポイントへ接続されたスマートフォンや PC 等のブラウ ザから操作ができます。
④スマートフォンや PC 等のブラウザのアドレス画面で

「prjballxx.local」と打ち込んで「Enter」キーを押してください。prjballXX の XX 部分はアクセスポ

イント名の prjballXX の XX 部分と同じです。XX 部分は ESP-WROOM-02 の MAC アドレスの一部分 の固有な英数字です。
⑤「ProjectionBall Remote」画面が表示されたら、接続完了です。 再びサーバモードで接続したい場合は「Wifi」タブの「SSID」「PASS」で適当な文字を設定します。。 ※適当な文字を入力することでアクセスポイントが見つからないため、サーバモードになります

7-3. ProjectionBall Remote 使用方法

「ProjectionBall Remote」画面の使用方法について説明します。


「ProjectionBall Remote」画面表示直後は「Control」「Data」「Mode」「Pattern」「Config」「Info」の 6 つ のカテゴリで表示されます。

◆「Control」カテゴリ

・「Start/Stop」
描画の一時停止は「Stop」、再開は「Start」を押してください。

・「Angle」
描画の角度を変更する際に使用します。
角度を 0~359°の範囲で入力します。
角度分解能は 3°です。


◆「Data」カテゴリ

・「Internal/Memory Data」
内蔵描画パターンから描画する場合は「Internal Data」を押します。
描画データの入った microSD から描画する場合は「Memory Data」を押します。 ※microSD が挿入されていない場合や描画データが入っていない場合は「Memory Data」を押し た場合、描画が停止します。


◆「Mode」カテゴリ

・「Animation」
－microSD カード無：リサージュ曲線描画
－microSD カード有：アニメーション描画(frame**.csv のファイルを順番に読込します)

・「Rotation」
回転しながら描画するモードです。

・「One-stroke」
一筆書きで描画するモードです。

・「Always-on」
常時データを描画するモードです。

・「Analog Watch」
アナログ時計を表示するモードです。

・「Digital Watch」
デジタル時計を表示するモードです。

・「Date」
日付を表示するモードです。

・「String」
英数字の文字列を表示するモードです。初期値は「Hello」です。 任意の文字列を「String」欄に記入して「Send」ボタンを押すと任意の文字列を描画できます。 ※6 文字以上の場合は自動的にスクロールされて描画されます。


◆「Pattern」カテゴリ
microSD カード有でも該当する描画データがない場合は描画が停止します。

・「Star/Data0」
－microSD カード無：内蔵データの星が描画されます。 －microSD カード有：data0.csv のファイルが描画されます。

・「Star/Data0」
－microSD カード無：内蔵データの星が描画されます。 －microSD カード有：data0.csv のファイルが描画されます。

・「Arrow/Data1」
－microSD カード無：内蔵データの矢印が描画されます。 －microSD カード有：data1.csv のファイルが描画されます。

・「Mail/Data2」
－microSD カード無：内蔵データのメールが描画されます。 －microSD カード有：data2.csv のファイルが描画されます。

・「Smile/Data3」
－microSD カード無：内蔵データのスマイルが描画されます。 －microSD カード有：data3.csv のファイルが描画されます。

・「Sun/Data4」
－microSD カード無：内蔵データの太陽が描画されます。 －microSD カード有：data4.csv のファイルが描画されます。

・「Cloud/Data5」
－microSD カード無：内蔵データの雲が描画されます。 －microSD カード有：data5.csv のファイルが描画されます。

・「Rain/Data6」
－microSD カード無：内蔵データの傘が描画されます。 －microSD カード有：data6.csv のファイルが描画されます。

・「Snow/Data7」
－microSD カード無：内蔵データの雪が描画されます。 －microSD カード有：data7.csv のファイルが描画されます。

・「Thunder/Data8」
－microSD カード無：内蔵データの雷が描画されます。 －microSD カード有：data8.csv のファイルが描画されます。

・「Heart/Data9」
－microSD カード無：内蔵データのハートが描画されます。 －microSD カード有：data9.csv のファイルが描画されます。


◆「Config」カテゴリ
WiFi モジュールのアクセスポイント設定や日付、時刻の設定をします。

・「WiFi AP Mode Setting」
アクセスポイントを経由して接続するクライアントモードを使用する際にアクセスポイント名 (SSID)とパスワード(PASS)を設定します。入力して「SAVE」を押すと設定が保存されます。

・「Set Date」
日付を設定する場合に「Send」を押します。日付はスマートフォンや PC 等のブラウザから取 得した日付が自動的に入力されます。
※日付が正しく表示されない場合は操作しているスマートフォンや PC 等の日付を確認してくだ さい。

・「Set Time」
時刻を設定する場合に「Send」を押します。時刻はスマートフォンや PC 等のブラウザから取得 した時刻が自動的に入力されます。
※時刻が正しく表示されない場合は操作しているスマートフォンや PC 等の時刻を確認してくだ さい。


◆「Info」カテゴリ
Wifi モジュールのバージョンや Web サイトリンクが表示されます。


8. 任意データ描画方法

SD カードに描画データを入れて基板上のスロットし、任意図形を描画できます。

8-1. SD カード描画仕様
- SD カードが挿入されていない状態では自動的に本体内蔵のメモリデータから描画を行います。
- SD カード挿入されており、描画データが入っていない場合やファイルが破損している場合はエラー となり、何も描画されません。
-パターン描画仕様
・パターンスイッチ切り替えで最大 10 種類の描画が可能となります。 ・モードスイッチ切り替えで常時点灯、回転、 一筆書きの 3 種類から選択可能です。 ・1 つのファイル当たりの座標最大数は 200 個です。

・ファイル名は半角英数字で data0.csv data1.csv data2.csv data3.csv…data9.csv です。 -アニメーション描画仕様
・frame0 から frame**(最大**は 17 まで)に少しずつ異なる描画データを入れることでパラパラ漫 画のようにアニメーション描画が可能となります。
・SD カードに該当するファイルを入れ、モードスイッチ SW4 下、SW5 下にセットするとアニ メーション描画が開始されます。
・1 つのファイル当たりの座標最大数は 200 個です。

・ファイル名は半角英数字で frame0.csv frame1.csv・・・ frame18.csv にしてください。 ・約 300msc 毎に自動で frame0 から frame1、frame2 と SD カード内にあるファイル数に応じて順 番に描画データが切り替わります。
・最後のファイルで frame0 に戻り、繰り返し動作します。

8-2. 描画データ作成方法
本節では専用の描画データ作成ソフトを利用した描画データ作成方法について説明します。 描画ソフトは下記の URL からダウンロードしてください。

http://projectionball.jp/share/PBS.zip pass: crescent

・動作環境は Windows .NetFramework4.5 以降インストール済み PC ・インストーラ不要で PBS2.exe をダブルクリックで起動します。 ・専用描画ソフトウェアを使用した描画データ作成方法流れ
1) ソフトウェアを起動させてください。
2) 左クリックで新しい座標を配置し、好きな図形を作成してください。逆に削除する場合 は右クリックで座標を削除できます。
3) 曲線部や複雑な図形は座標を細かく配置してください。また、開始点と終了点が近い位 置になるように設定してください。
4) 完成したら、「ファイル」→「名前を付けて保存」→「pbs ファイル」として保存します。

5) 「ファイル」→「csv エクスポート」→「data0.csv」を選択し、エクスポートします。
6) 「data0.csv」ファイルを SD カードに保存し、SW2 下、SW3 下、SW4 上、SW5 上にセ ットし、電源を入れると図形が描画されます。
※注意 pbs ファイルを SD カードに保存しても描画できません。csv ファイルをエクス ポートして SD カードに保存してください。

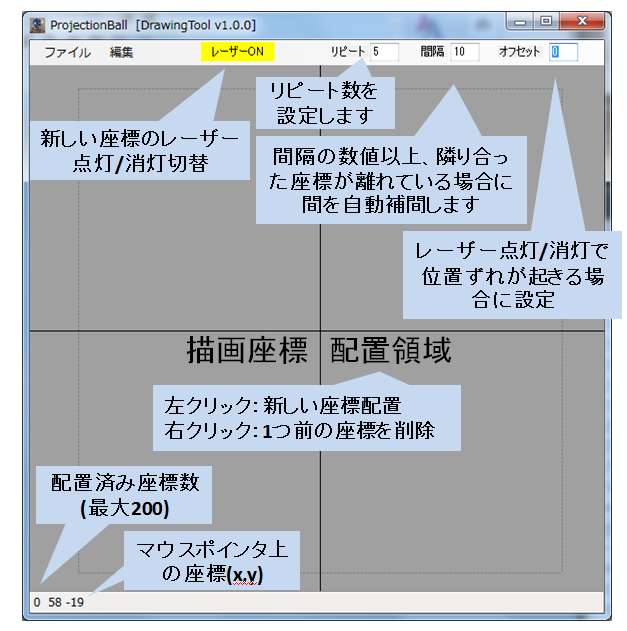
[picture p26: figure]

・リピート数が大きくなると精度は上がりますがフレームレートが荒くなります。逆にリピー ト数が小さいと精度は悪くなりますが、フレームレートは上がります。リピート数 5 が標準 で複雑な図形の場合は 8~12 に設定します。逆に簡単な図形の場合はリピート数を 3~5 に設定 します。
・途中の座標を移動させたい場合は「Ctrl」キーを押しながら移動させたい座標部分をドラッグ

すると途中の座標を移動させることができます。
・新しく座標を配置する場合、「Shift」キーを押しながら左クリックすると、レーザーOFF モー ドで座標が配置されます。
・開始点と終了点が近い位置にできない場合は「レーザーON/OFF」をクリックし、レーザー点 灯を OFF にして、終了点が開始点付近になるように消灯の座標を配置してください。 ・描画したい図形の画像ファイルがある場合は「編集」→「背景読込」で背景を配置します。 ※サイズが合わない場合は画像ファイルを「ペイント」等で編集してリサイズしてください。 ・描画座標数が 200 点を超えるメッセージがエクスポート時に出た場合は座標数を減らすか、 間隔を初期値の 10 から 20 など大きな値に設定してください。

-描画データ精度向上の工夫について
・鋭角に描画したい場合は角の部分の座標を数回連続して、同じ個所に配置すると角が綺麗に 描画されます。
・鋭角部分は遠回りさせて描画させ、遠回り部分を「レーザーOFF」させることで綺麗に描画す る方法も可能です。

8-3. 描画データ仕様
描画データの仕様について説明します。専用の描画ソフトで作成した csv ファイルは下記の仕様を満 たしています。専用の描画ソフトを使用しない場合に参考にしてください。

・最初の 1 行目は描画定義を行う数値を入れます。1 行目 1 列はリピート数を入れます。
1 行目 2 列、3 列は 0 を記入してください。5 が標準で複雑な図形の場合は 8~12 に設定します。 簡単な図形の場合はリピート数を 3~5 に設定します。 ・リピート数が大きくなると精度は上がりますがフレームレートが荒くなります。 逆にリピート数が小さいと精度は悪くなりますが、フレームレートは上がります。 ・2 行目から座標データを半角数字で入力します。
・1 列目がレーザー点灯有無で 0 が消灯、1 が点灯です。
・2 列目は X 座標、3 列目は Y 座標です。
・座標は(0,0)を中心として最大(±150,±150)を目安に作成してください。 ・描画がスタートすると 2 行目から 3 行目、4 行目と順番にレーザー光が移動します。 ・空欄を見つけると最後のデータとして判断し、2 行目に戻り再度描画を開始します。 ※専用描画ソフトウェアの場合は自動で下記のルールに従ったデータとなります

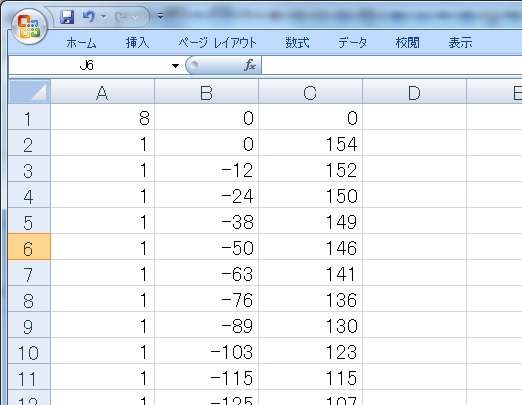
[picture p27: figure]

9. WiFi モジュール書き換え方法

ProjectionBall 本体に WiFi 通信するための ESP-WROOM-02 を搭載しています。工場出荷時の ESP-WROOM-02 コードは下記のサイトで公開されています。必要に応じて、ESP-WROOM-02 のアップ デートや追加して自作コードを入れ込むことも可能です。

https://github.com/meerstern/prjball-wifimodule2
また、ProjectionBall で使用している RX、TX ポート以外の IO ピンは外部 EX ポートからアクセス可能 です。必要に応じて別途 LED やシリアル通信機器を接続することが可能です。

9-1. Arduino 開発環境準備
ESP-WROOM-02 のファームウェアのアップデートや自作コードを入れ込む際には Arduino 開発環境 を使用します。
①Arduino 開発環境をパソコンへインストールします。
②Arduino 開発環境を起動させ、「ファイル」→「開発環境」をクリックします。 ③「設定」タブの「追加ボードマネージャの URL」へ下記の URL を追加します。

http://arduino.esp8266.com/stable/package_esp8266com_index.json

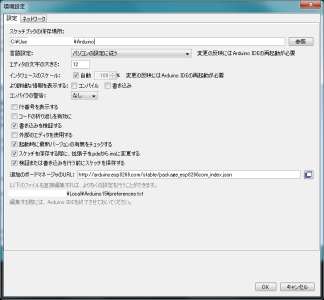
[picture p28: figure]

④「ツール」→「マイコンボード」→「ボードマネージャ」から一番下までスクロールして、「esp8266 by ESP8266 Community」を選択し、インストールをクリックします。

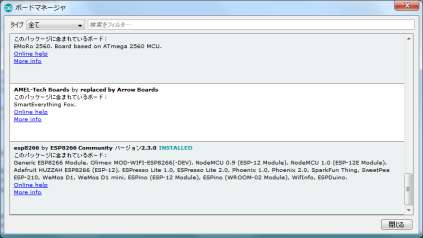
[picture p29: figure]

⑤「ツール」→「マイコンボード」→「Generic ESP8266 Module」をクリックします。 ⑥「ツール」→「マイコンボード」で設定を下記のように行います。 シリアルポートは書き込み時に ESP-WROOM-02 と接続しているシリアルポートを選択します。


9-2. Arduino 開発環境からの書き込み
Arduino 開発環境から ESP-WROOM-02 へファームを書き込む際には USB シリアル変換モジュール等 が必要です。 別途ご用意ください。

USB シリアル変換モジュール(AE-FT234X ) http://akizukidenshi.com/catalog/g/gM-08461/

①WiFi UART TX ピンと WiFi UART RX ピンにジャンパピンを外し、

USB シリアル変換モジュールと ProjectionBall 本体の ESP-WROOM-02 を接続します。
USB シリアル変換モジュールの GND と WiFi UART GND ピンを接続します。

USB シリアル変換モジュールの TX と WiFi UART RX ピンを接続します。 USB シリアル変換モジュールの RX と WiFi UART TX ピンを接続します。

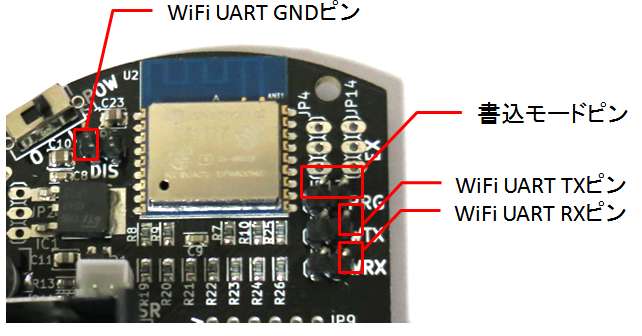
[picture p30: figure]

②デバイスマネージャ等から USB シリアル変換モジュールのポート番号を確認します。 ③下記のサイトから最新の WiFi モジュールのファームコードをダウンロードして、「ESP8266.ino」フ ァイルを開きます。

https://github.com/meerstern/prjball-wifimodule2
④USB シリアル変換モジュールのポート番号を設定します。 「ツール」→「シリアルポート」から接続先のポートを選択します。 ⑤書き込みモードピンにジャンパを接続し、書き込みモードピンをショートさせます。

⑥ProjectionBall 本体の電源を入れます。
⑦書き込みボタンを押してファームを書き込みます。

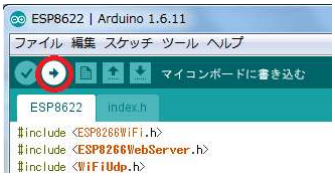
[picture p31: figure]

⑧書き込みが終了したらアップデートです。
初回、書き込み時はエラーが出る場合があります。
エラーが出る場合は①から作業を確認しながら再度、試行してください。
⑨WiFi UART TX ピン(必要に応じて WiFi UART RX ピン)にジャンパピンをセットしてください。

10. 外部機器連携方法

ProjectionBall 本体の UART ポートへ他の機器の UART ポートからコマンドを送信することで描画パタ ーンや描画モードの切り替え、描画の一時停止や描画データの再読み込みが可能です。 必要に応じてピンヘッダや配線を行い、他の機器と接続してください。基板上の TX を他機器の RX 端 子、基板上の RX を他機器の TX 端子に接続し、GND も合わせて接続してください。
PC 等 か ら コ マ ン ド を 送 信 す る 場 合 は USB シ リ ア ル 変 換 モ ジ ュ ー ル (AE-FT234X

http://akizukidenshi.com/catalog/g/gM-08461/ )等を使用し、Teraterm 等の COM ソフトウェアを用いてコマ ンドを送信してください。
コマンドを送信後、リターンキー(改行)送信でコマンドが実行されます。UART の電圧は 3.3V です。 RS232C とは異なります。また、ボーレートは 9600bps に設定してください。
※外部機器連携の場合は UART ポートが競合するため、WiFi モジュールからのコマンド指令は使用で きません。

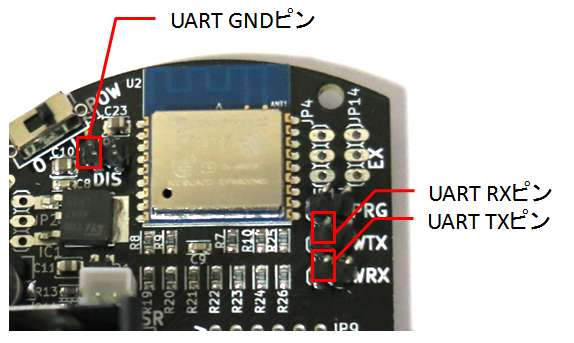
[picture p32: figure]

表 1 UART コマンド一覧

コマンド名 | コマンド | 説明
スタート指令 | srt | 描画をコマンドで停止した場合に再度、再開時に使用します。
ストップ指令 | stp | 描画を停止させる場合に使用します。
パターン 0 指令 | sw0 | SD カード無 星パターン、SD カード有 data0.csv 描画
パターン 1 指令 | sw1 | SD カード無 矢印パターン、SD カード有 data1.csv 描画
パターン 2 指令 | sw2 | SD カード無 メールパターン、SD カード有 data2.csv 描画
パターン 3 指令 | sw3 | SD カード無 スマイルパターン、SD カード有 data3.csv 描画
パターン 4 指令 | sw4 | SD カード無 太陽パターン、SD カード有 data4.csv 描画
パターン 5 指令 | sw5 | SD カード無 雲パターン、SD カード有 data5.csv 描画
パターン 6 指令 | sw6 | SD カード無 傘パターン、SD カード有 data6.csv 描画
パターン 7 指令 | sw7 | SD カード無 雪パターン、SD カード有 data7.csv 描画
パターン 8 指令 | sw8 | SD カード無 雷パターン、SD カード有 data8.csv 描画

パターン 9 指令 | sw9 | SD カード無 ハートパターン、SD カード有 data9.csv 描画
アナログ時計指令 | awt | アナログ時計表示モードに切り替わります。
デジタル時計指令 | dwt | デジタル時計表示モードに切り替わります。
日付表示指令 | dym | 日付表示モードに切り替わります。
文字列表示指令 | stm | 任意文字列表示モードに切り替わります。
文字列セット指令 | stg=X | X に英数字文字列を入れることで任意の英数字を表示します。 X は最大 30 文字程度です。
時刻セット指令 | tim=XXYYZZ | UART を介して時刻をセットします。 例 tim=213000 21 時 30 分 00 秒
時刻取得指令 | tim? | 現在、ProjectionBall 内部で保持されている時刻が UART で返さ れます。
日付セット指令 | day=XXYYZZ | UART を介して日付をセットします。 例 day=170401 17 年 4 月 1 日
日付取得指令 | day? | 現在、ProjectionBall 内部で保持されている日付が UART で返さ れます。
アニメーションモード指令 | frm | SD カード無 リサージュ曲線 SD カード有 アニメーション(frame**.csv)となります。
回転モード指令 | rot | 回転するアニメーション描画モードに切り替わります。
一筆書きモード指令 | str | 一筆書きアニメーション描画モードに切り替わります。
常時点灯指令 | alw | 常時点灯の描画モードに切り替わります。
中央位置設定コマンド | cen=X,Y | X と Y にそれぞれ数字を入れることで、現在の描画座標中心を 相対移動するコマンドです。大きな値を設定した場合、描画が 正しく行われない場合があります。 例 cen=20,-30
角度設定コマンド | deg=X | X に 0°から 360°までの値を入れることで、3°間隔で描画図形を 回転させるコマンドです。 例 deg=135
再読み込み指令 | rst | SD カードを入れ替えた際に再度、読込を実行するコマンドで す。
アニメーション描画 フレーム指定コマンド | fno=X | X に 0 から最大 18 までの値を入れることで、指定したアニメー ションのコマを描画します。
アニメーション描画 フレーム一時停止コマンド | fpa | アニメーション描画時の描画データの自動送りを停止します。 再度、同コマンドを実行することで自動送りを再開します。

11. レーザーモジュール仕様

標準では安全面を考え、1mW 以下の 3.3V 駆動の赤色レーザーモジュールを使用しています。他のレー ザーモジュールに交換する場合は同じ 3.3V 駆動のレーザーモジュールが使用可能です。供給できる電流 は 250mA が設計上の最大電流です。標準品以外のレーザーモジュール使用による不具合や故障はサポー トできません。

12. 調整/トラブルシューティング

不具合等が発生した場合は下記を参考にしてください。
◆電源 LED は点灯するが、描画が開始されない
－一時停止モードの場合は解除してください
ProjectionBall 本体、左上と左下を同時に手のひらでタッチしてください。再度、左上と左下を同 時に手のひらでタッチすると描画を再開します。パターンボタンとモードボタンの同時押しでも同 様です。
－USB 電源の電流が充分足りているか確認してください。
USB 充電用のアダプタ等(電圧 5V、電流 1.2A 以上)に接続して使用してください。

◆モードやパターン、時刻等がリセットされる
USB 電源がない状態で数カ月以上保持することが可能です。 モードや時刻等が保持されない場合は電池を交換してください。
交換電池 CR2032 x1 ※プラスマイナスの極性に注意して交換してください。

◆WiFi のアクセスポイントが表示されない、接続できない －ProjectionBall 本体の WiFi 無効化ピンにジャンパピンがないことを確認してください。 WiFi 無効化ピンにジャンパピンが挿入されている場合、電波が停波し接続できません。 －周辺に他の WiFi 電波が複数ある場合は混信や干渉で接続できない場合があります。 ProjectionBall 本体に PC やスマートフォンを近づけて接続してください。

◆描画が欠ける
－スタンドや球体等にレーザー光が当たって、遮られていないか確認してください。 －描画の中心位置がずれている場合があります。
描画中心位置がずれるとフレーム部分にレーザーの光軸が干渉し描画が欠けます。まずレーザー光 軸がミラーの中心で反射するようにモータやレーザーモジュールの位置を調整してください。それ でも中心に来ない場合は可変抵抗を調整します。
描画中心調整用の可変抵抗 VR1,2 を+ドライバで調整してください。調整は微小角度、回してくださ い。モータ 2 のミラー(裏側)の中心にレーザー光が当たっていない場合は VR1 を調整してモータ 1(X 軸方向)の中心を調整します。モータ 2 から出たレーザー光が基板に引っかかる場合は VR2 を調整し

てモータ 2(Y 軸方向)の中心を調整します。

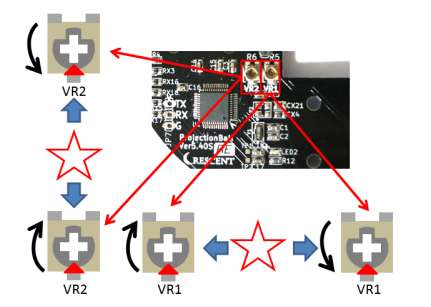
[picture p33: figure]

◆形状がでたらめに描画される or 描画がきれいでない
―電源の電流が足りない場合や USB 充電アダプタの安全回路により電流が制限されて正常に動作しな い場合があります。別の USB 電源を試してください。
―ミラーの位置磁石の中心とエンコーダ IC(エンコーダ基板の黒いチップ)の中心が一致しているか確 認してください。また磁石とエンコーダ IC との距離を 5mm ほどか確認してください。逆に近すぎ る場合は接触や磁力が強すぎて綺麗に描画できない場合があります。

◆エラー黄色 LED 点灯して、停止する
―モータ 1、モータ 2 がコネクタに正しく接続されているか確認してください。エンコーダ基板が正し く半田付けされているか確認してください。また、レーザーモジュールの筺体の金属がエンコーダ 基板の半田付け部分と接触してショートしていないか確認してください。

◆ミラーモジュール磁石位置調整方法
出荷時にこの調整は既に行っています。ミラーモジュールから磁石を取り外さないでください。 万一、ミラーモジュールから磁石を外してしまった場合に以下の手順で磁石位置調整を行ってくださ い。
ミラーモジュールのモータ軸取り付け部と逆側(下図赤枠部)に位置検出用のﾈｵｼﾞﾑ磁石が取付けて あります。このﾈｵｼﾞﾑ磁石は一般的な磁石と異なり、軸方向に NS 極が分かれています。N 極と S 極の 境界をセンサで検出し、位置を読み取っています。鏡の反射面とこの磁極の角度がずれると意図した 場所で描画できません。

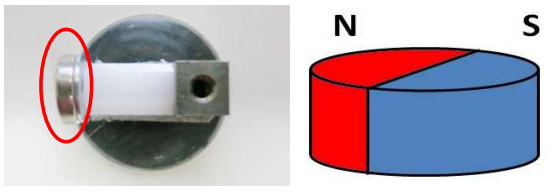
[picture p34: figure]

※片方が正常に取り付けられている場合は、磁石面を向かい合わせて 2 つのミラー面が水平になるよ うに磁石を固定して調整することが可能です。

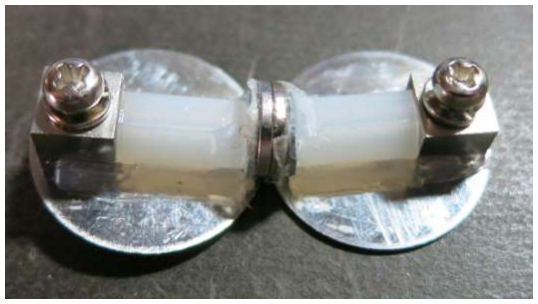
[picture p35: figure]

① ミラーモジュールの磁石部分を下向きにして方位磁石の中心にミラーモジュールを置く(長時間 置くと方位磁石が狂うため注意)。

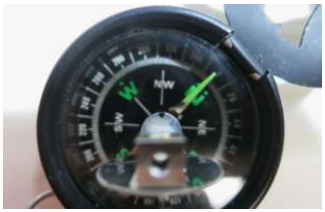
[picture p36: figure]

② 下図のように方位磁石の N 極が左を向くようにワッシャに吸着した磁石を回転させ、方位磁石の 角度とミラー面が一致させる。調整し終わったら、テープ等で固定する。

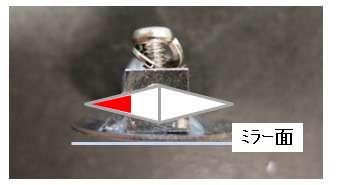
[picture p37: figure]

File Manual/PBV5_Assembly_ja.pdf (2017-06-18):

# Projection Ball IoT

v5.6S

# 組立手順書

改訂履歴

第 1 版 | 2017/05/12 | 新規作成

ProjectionBall 組立手順書 | 2

目次

1. 概要

本資料の対象は Projection Ball の組立/販売を行う者を想定している。

2. 部品リスト
No. | 名称 | 個数 | 備考
1 | メイン基板 | 1 | 実装済み
2 | エンコーダ基板 | 2 | 実装済み
3 | エンコーダ基板固定用 L 字ピンヘッダ | 2 | 1 列 x6 ピン
4 | DC モータ | 2
5 | 積層セラミックコンデンサ | 2 | モータノイズ対策用
6 | PH コネクタ付きケーブル | 3 | モータ用 2 つ、レーザー用 1 つ
7 | ジャンパ | 2 | Wifi 用
8 | CR2032 | 1
9 | レーザーモジュール | 1
10 | ミラーユニット | 2 | ミラー、磁石、ネジ付き
11 | 結束バンド | 5
12 | 固定スポンジ | 7 | 基板用に 4 つ、三脚用に 3 つ
13 | 球体 | 1 | 上下で 1 つ
14 | 三脚 | 1 | フレーム、
15 | microUSB ケーブル | 1

3. ミラーモジュール組立

3D プリンタで作成したミラーモジュールを組み立てる場合の手順を説明する。 ①ミラーを固定する

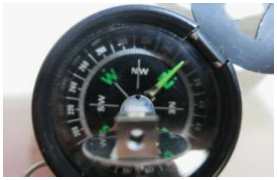
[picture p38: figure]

②ナットを溝に入れる


③磁石を下記の磁極方向に注意して方位磁石の N が真左を向くように固定する ④ミラーと磁石を瞬間接着剤で固定する

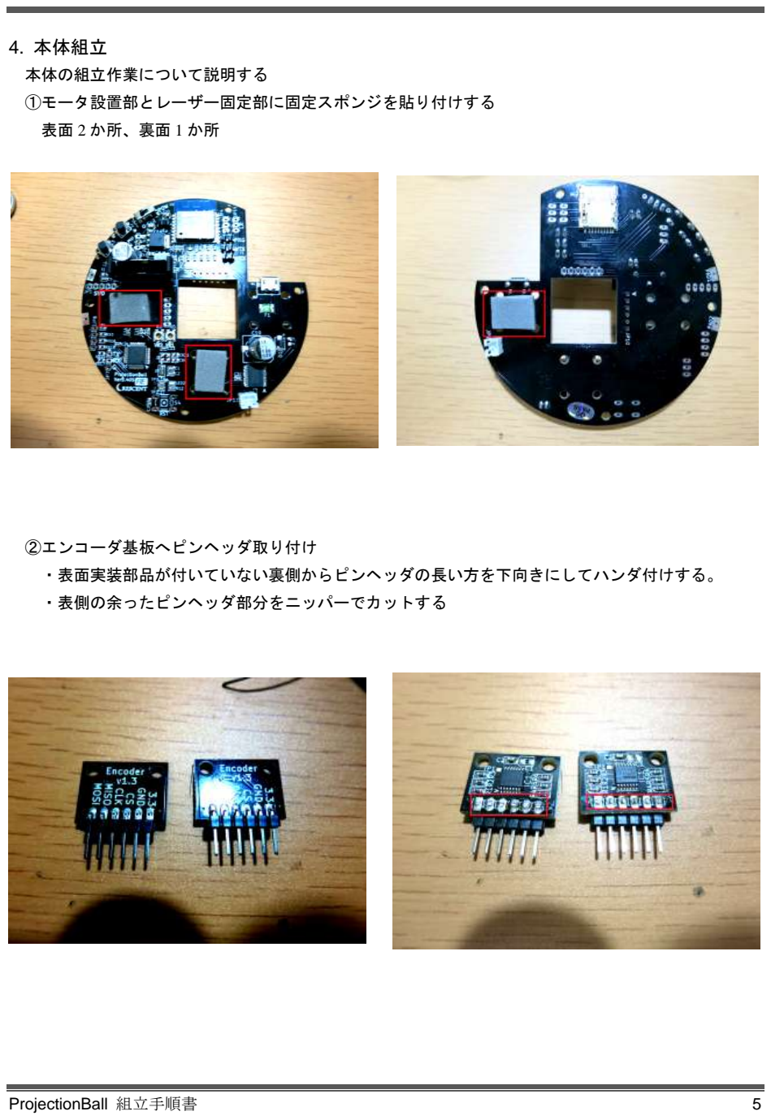
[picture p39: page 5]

4. 本体組立

本体の組立作業について説明する
①モータ設置部とレーザー固定部に固定スポンジを貼り付けする 表面 2 か所、裏面 1 か所

②エンコーダ基板へピンヘッダ取り付け
・表面実装部品が付いていない裏側からピンヘッダの長い方を下向きにしてハンダ付けする。 ・表側の余ったピンヘッダ部分をニッパーでカットする

③エンコーダ基板をメイン基板へハンダ付けする
・エンコーダ基板のチップを内側の穴に向けてメイン基板の上下にエンコーダ基板をハンダ付け ・反対側の余分なピンをニッパーでカットする

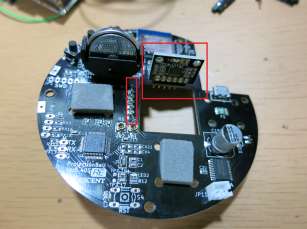
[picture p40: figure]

④モータへ PH ケーブルをハンダ付けする

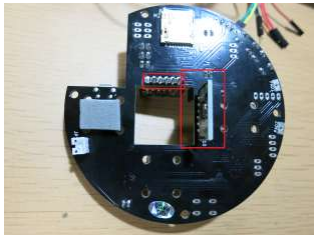
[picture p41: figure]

・モータへ 0.1uF の積層セラミックコンデンサをハンダ付けする ・ケーブル色に注意してモータへ PH ケーブルをハンダ付けする


⑤タッチセンサ用のケーブルをハンダ付けする
・メイン基板スイッチ側を表面へケーブルをハンダ付けする ・メイン基板マイコン側を裏面へケーブルをハンダ付けする

⑥レーザーモジュールに PH ケーブルをハンダ付けする ・PH ケーブルのケーブル色に注意して、ハンダ付けする

⑦レーザーモジュールを取り付け
・メイン基板左側中央にレーザーモジュールを取り付けする ・レーザーモジュールの PH コネクタをボタン電池横の PH コネクタへ接続する


⑧モータ取り付け
・モータを立てた状態で結束バンドを用いて 2 か所固定する。 ・メイン基板表面と裏面の 2 つモータを固定する
・固定後はペンチで端を摘みながら捻じって強固に固定する



⑨ミラーモジュールを取り付けする


・ミラーモジュールとモータ筺体が接触しないように隙間を 1mm 程度空けて取り付ける ・エンコーダ基板とミラーモジュールが接触しないように同様に隙間があることを確認する

5. 調整

5-1. 描画中心位置調整
－スタンドや球体等にレーザー光が当たって、遮られていないか確認してください。 －描画の中心位置がずれている場合があります。
描画中心位置がずれるとフレーム部分にレーザーの光軸が干渉し描画が欠けます。まずレーザー光 軸がミラーの中心で反射するようにモータやレーザーモジュールの位置を調整してください。それ でも中心に来ない場合は可変抵抗を調整します。
描画中心調整用の可変抵抗 VR1,2 を+ドライバで調整してください。調整は微小角度、回してくださ い。モータ 2 のミラー(裏側)の中心にレーザー光が当たっていない場合は VR1 を調整してモータ 1(X 軸方向)の中心を調整します。モータ 2 から出たレーザー光が基板に引っかかる場合は VR2 を調整し てモータ 2(Y 軸方向)の中心を調整します。


6. パッキング
